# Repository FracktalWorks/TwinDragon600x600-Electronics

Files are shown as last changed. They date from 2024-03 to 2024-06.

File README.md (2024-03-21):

# TwinDragon600x600-Electronics
Electronic description, pinout and manuals for the electronics used in Twin Dragon 600x600x600 (Enhanced Size)

### For the Combination of BTT Manta M8P V2.0 + RPi CM4 + RP2040 based toolboard

Pin Configurations, jumper selection, CanBus and multi-MCU wiring to RPi CM4 embedded onto BTT Manta M8P V2.0 for Twin Dragon 600x600x600

Components used:
1. BTT Manta M8P V2.0 - 1
2. RPi CM4 (embed onto BTT Manta M8P V2.0) - 1
3. RP2040 based Can Module/Toolboard - 2
4. TMC5160 Stepper drivers - 4
5. TMC5160T Plus Z driver - 1
6. TMC2209 stepper drivers - 2 (External) + 2 (Present on the Toolboards)
7. BTT HDMI5 Touch Display

## Setting up BTT Manta M8P V2.0 + RPi CM4 + RP2040 based toolboard

After powering on the M8P, the LED on the bottom left corner will light up to indicate normal power supply. The VUSB jumper in the center is for selecting power - it should only be shorted when powering the board via USB or supplying power out via USB.



### Other Initial preparation and setting up jumpers

#### TMC Driver SPI Mode



The first row are the defined pin for the drivers, which are either high or low when shorted or unshorted to establish different mode of communication. The second row are defined with the SPI modes, with the namings of 'MISO', 'CS', 'SCK' and 'MOSI' when read from left to right. Since we use the TMC5160 driver, it specifically operates only on the SPI mode. Insert the jumpers corresponding to its parallel pins only on the 1st and the 2nd row as shown in the image.

#### TMC Driver UART Mode



The given set of pin to short is the CS pin that enables only the uart mode.

#### Driver Voltage selection

For High Voltage selection(48V):



Since the TMC5160 operates only on SPI mode, which is specifically for achieving faster communication and higher speeds, it needs an operating voltage of around 48V. The manta M8P has seperte pins for regular voltage of 24V and high voltage of 48V, that is to be jumped to the common pin of voltage supply to the drivers. We jump the HV pin in the left to the middle pin of supply in order to provide 48V to the drivers, as shown in the image above.

For normal Voltage selection (24V):



This voltage selection can be used when using a regular TMC2209 on the UART mode

#### Setting up jumper for probe activation

BTT Manta M8P V2 0 ABL Connections

The pin for probe used here is the IND-probe pin on Manta M8P V2.0, and the jumpers are placed on the two pins beside the probe pins, and other three perpendicular pins to its right, where the top two are to jumped together to activate the probe pin, as shown in the image above, to enable 24V/5V supply to the ABL board. The three columns of the pins starting from the top are 5V, 12V, 24V Respectively.

#### Setting up Jumper for CANBUS communication



At the left of the CAN pin, a small jumper is to be placed on the pins that mention '120R' depicting the 120 ohms resistance that is applied on the CAN Low and High communication pins. This is a crucial pin for the setting up of the CAN communication of the motherboard and toolboard.

## Wiring and Connections

Twin Dragon 600 CM4 M8P V2 0 - Wiring

The overall connections of all the Electrical and Electronic components are present in the image above

### BTT Manta M8P V2.0 Pin connections

Twin Dragon 600x600 with M8P V2 0 Wiring

## Dragon ToolBoard Pinout Mappings

WhatsApp Image 2024-03-20 at 14 31 21

WhatsApp Image 2024-03-20 at 14 31 21 (1)

## Guide to place the connectors on the Carriage Minifit Board

minifit board guide

## To setup Raspeberry Pi camera Rev 1.3, interfaced with RPi CM4 and BTT Manta M8P/M5P

In order to interface the Pi camera Rev 1.3 with the RPi CM4 and BTT Manta M8P/M5P, flip the board and check for a CSI1 camera slot, which should look like the image below



Instructions to attach the camera in BTT Manta M8P V2.0



Instructions to attach the camera in BTT Manta M8P V2.0

1. Now, boot up the board (including CM4), SSH into the CM4 and open the terminal
2. We will have to download a bin file into the boot folder of the CM4, below is the command to enter into the terminal.

`sudo wget https://datasheets.raspberrypi.com/cmio/dt-blob-cam1.bin -O /boot/dt-blob.bin`

If the above command does not work, try the following command:

`sudo wget https://datasheets.raspberrypi.com/cmio/dt-blob-cam1.bin -O /boot/firmware/dt-blob.bin`

3. Now, in the terminal, enter `sudo raspi-config` and select the option '3 Interface Options    Configure connections to peripherals'. Now select the first option 'P1 Camera      Enable/disable connection to the Raspberry Pi Camera'. A pop-up would appear where it asks to enable the camera. Make sure to select <yes> and exit the portal.

4. Now, in the terminal, type in `sudo nano /boot/config.txt` and make sure the settings are enabled

   `start_x=1
   gpu_mem=128`

   Note: make sure `#camera_auto_select=1` is commented out, or else it will not work.

For more clarifications, check out 'Julia TouchUI documentation' for more settings on Pi-camera

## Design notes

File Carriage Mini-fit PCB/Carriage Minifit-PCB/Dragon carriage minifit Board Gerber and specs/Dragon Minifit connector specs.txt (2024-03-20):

Dragon Carriage Board connector: 
 
Connector: 
Molex 6P 2x3 Minifit Jr. 4.2mm Connector: 
https://www.sunrom.com/p/6p-2x3-minifit-42mm-straight-female-pcb-header  
 
Housing: 
Molex 6P 2x3 Minifit Jr. 4.2mm Housing: 
https://www.sunrom.com/p/6p-2x3-minifit-42mm-male-housing  
 
Crimp Terminals: 
Molex 6P 2x3 Minifit Jr. 4.2mm Crimps: 
https://www.sunrom.com/p/crimping-pins-for-male-housing-minifit-42mm

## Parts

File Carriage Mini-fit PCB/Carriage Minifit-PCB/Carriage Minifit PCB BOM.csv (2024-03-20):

Qty | Designator | Footprint | Comment | LCSC Part # | Description | Value
1 | J1 | MOLEX_39281063 | 39281063 |  | Conn Wire to Board HDR 6Power POS 4.2mm Solder ST Top Entry Thru-Hole Mini-Fit Jr Bag Check availability | 39281063
1 | X1 | JST-XH-02-PACKAGE-LONG-PAD | JST-XH-02-PIN-LONG-PAD |  | JST XH Connector 2 Pin | JST-XH-02-PIN-LONG-PAD
1 | X2 | TERMINAL-BLOCK-4-PIN-3.5MM-LONG-PAD | TERMINAL-BLOCK-3.5MM-4-PIN-LONG-PAD |  | Terminal Block 3.5mm | TERMINAL-BLOCK-3.5MM-4-PIN-LONG-PAD

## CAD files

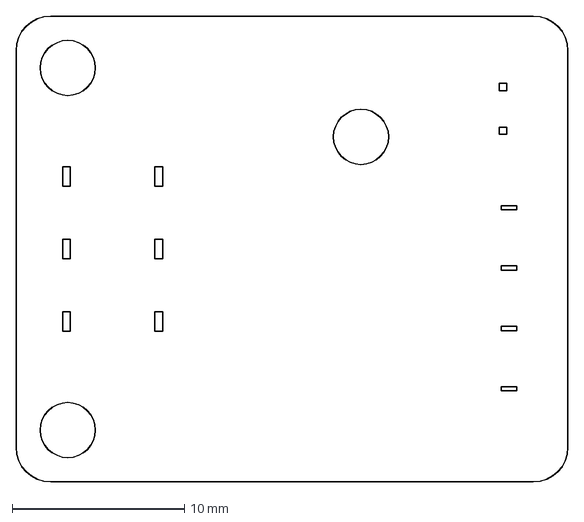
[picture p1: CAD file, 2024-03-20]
Carriage Mini-fit PCB/TD Carriage MINIFIT board.dxf
32.0 x 27.0 mm

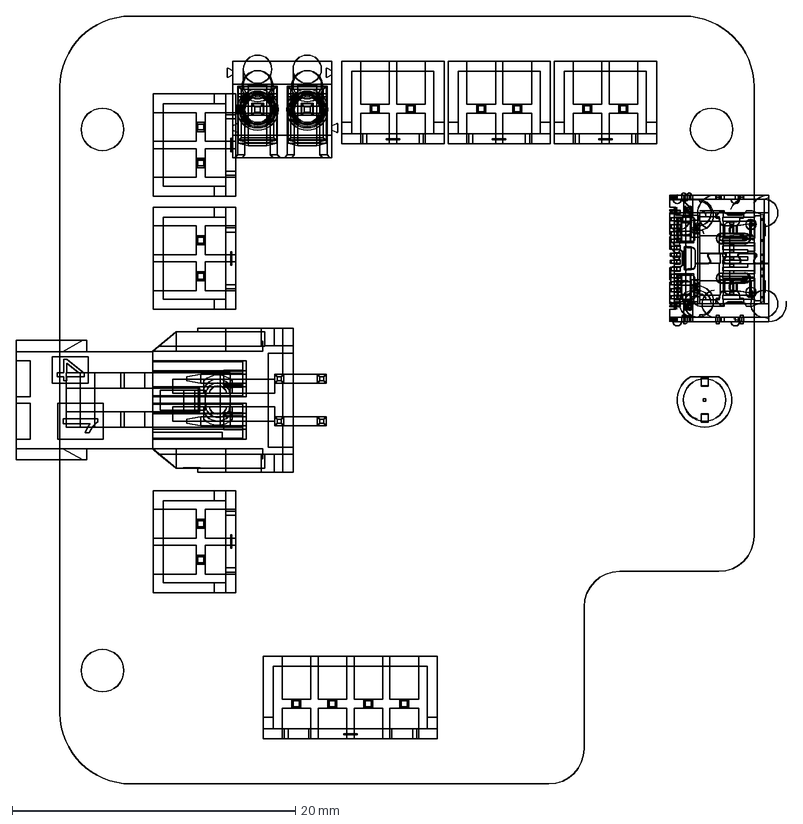
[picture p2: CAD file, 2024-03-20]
TD_Tool Board V2/PCB V2.1.dxf
54.4 x 54.2 mm

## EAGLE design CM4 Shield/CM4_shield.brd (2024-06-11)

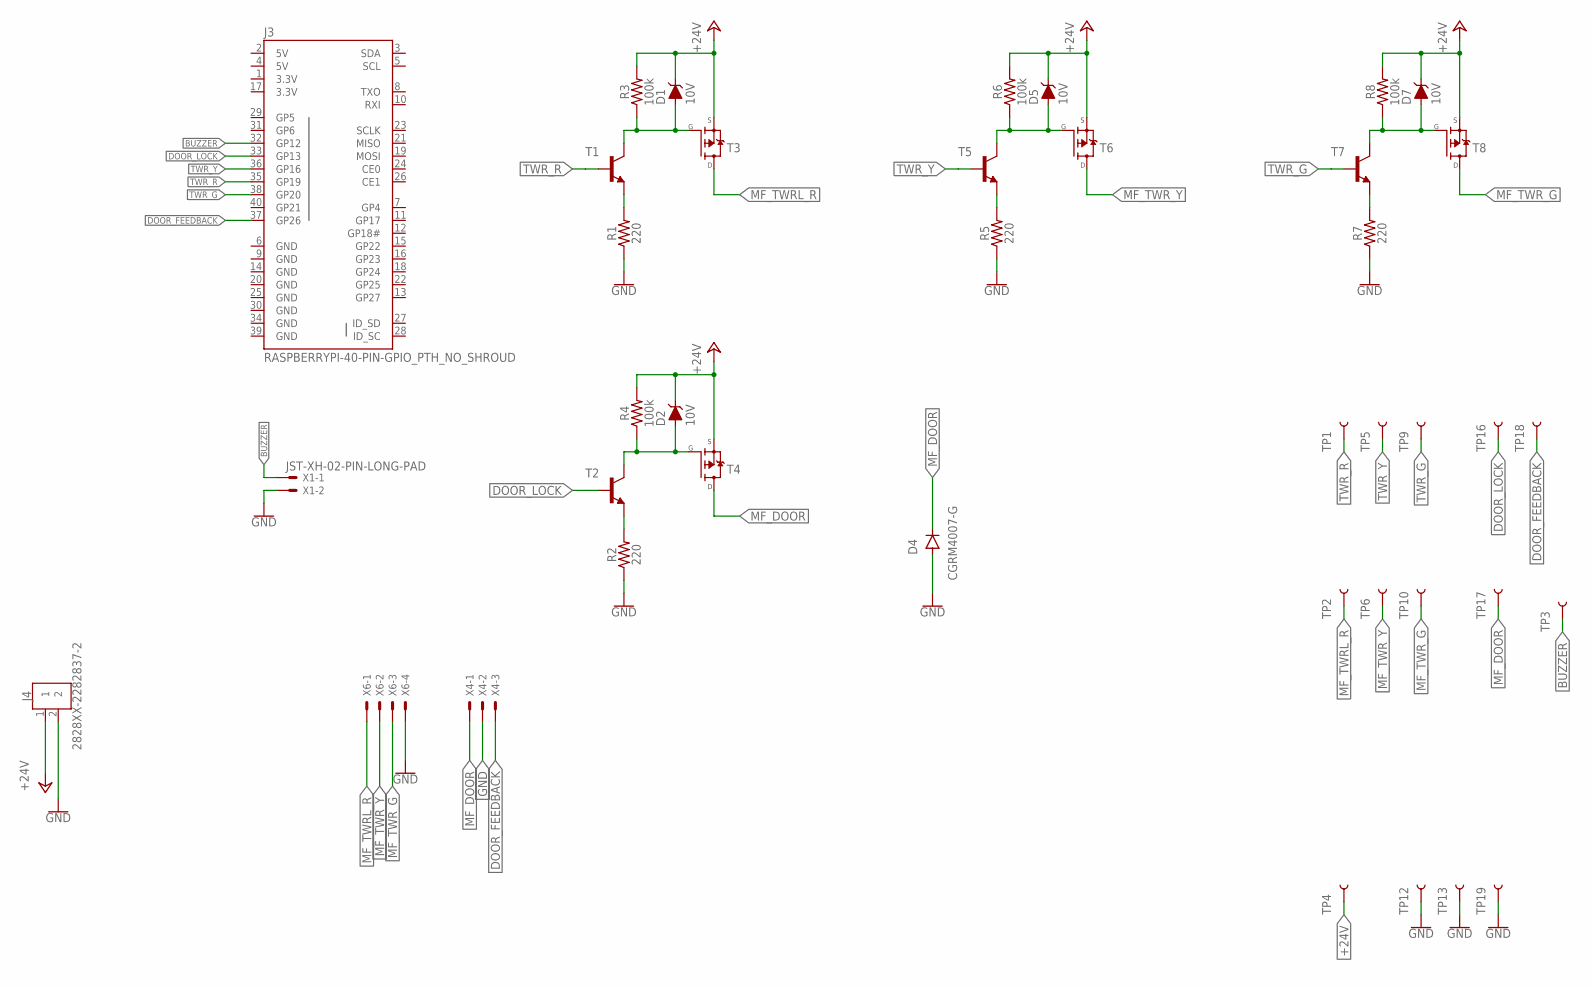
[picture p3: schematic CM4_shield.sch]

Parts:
D1, D2, D5, D7: 10V; PANASONIC_SMINI2-F5-B
D4: CGRM4007-G; SOD-123_MINI-SMA
J3: RASPBERRYPI-40-PIN-GPIO_PTH_NO_SHROUD; 2X20
J4: 2828XX-2282837-2; TERMBLK_508-2N
R1, R2, R5, R7: 220; 0603
R3, R4, R6, R8: 100k; 0603
T1, T2, T5, T7: MMBT3904LT1-NPN-SOT23-BEC; SOT23-BEC
T3, T4, T6, T8: MOSFET_P_SOT223; MOSFET_SOT223
TP1, TP2, TP3, TP4, TP5, TP6, TP9, TP10, TP12, TP13, TP16, TP17, TP18, TP19: TEST-POINT3X5; PAD.03X.05
X1: JST-XH-02-PIN-LONG-PAD; JST-XH-02-PACKAGE-LONG-PAD
X4: DOOR LOCK; JST-XH-03-PACKAGE-LONG-PAD
X6: TOWER LIGHT; JST-XH-04-PACKAGE-LONG-PAD

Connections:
3.3V: J3.1 (3.3V), J3.17 (3.3V)
5V: J3.2 (5V), J3.4 (5V)
+24V: D1.C, D2.C, D5.C, D7.C, J4.1, R3.2, R4.2, R6.2, R8.2, T3.3 (S), T4.3 (S), T6.3 (S), T8.3 (S), TP4.P$1
BUZZER: J3.32 (GP12), TP3.P$1, X1.1
DOOR_FEEDBACK: J3.37 (GP26), TP18.P$1, X4.3
DOOR_LOCK: J3.33 (GP13), T2.B, TP16.P$1
GND: D4.A, J3.6 (GND), J3.9 (GND), J3.14 (GND), J3.20 (GND), J3.25 (GND), J3.30 (GND), J3.34 (GND), J3.39 (GND), J4.2, R1.1, R2.1, R5.1, R7.1, TP12.P$1, TP13.P$1, TP19.P$1, X1.2, X4.2, X6.4
MF_DOOR: D4.C, T4.2 (D), T4.4 (D), TP17.P$1, X4.1
MF_TWRL_R: T3.2 (D), T3.4 (D), TP2.P$1, X6.1
MF_TWR_G: T8.2 (D), T8.4 (D), TP10.P$1, X6.3
MF_TWR_Y: T6.2 (D), T6.4 (D), TP6.P$1, X6.2
unnamed: R1.2, T1.E
unnamed: D5.A, R6.1, T5.C, T6.1 (G)
unnamed: D1.A, R3.1, T1.C, T3.1 (G)
unnamed: R5.2, T5.E
unnamed: D7.A, R8.1, T7.C, T8.1 (G)
unnamed: R7.2, T7.E
unnamed: D2.A, R4.1, T2.C, T4.1 (G)
unnamed: R2.2, T2.E
TWR_G: J3.38 (GP20), T7.B, TP9.P$1
TWR_R: J3.35 (GP19), T1.B, TP1.P$1
TWR_Y: J3.36 (GP16), T5.B, TP5.P$1

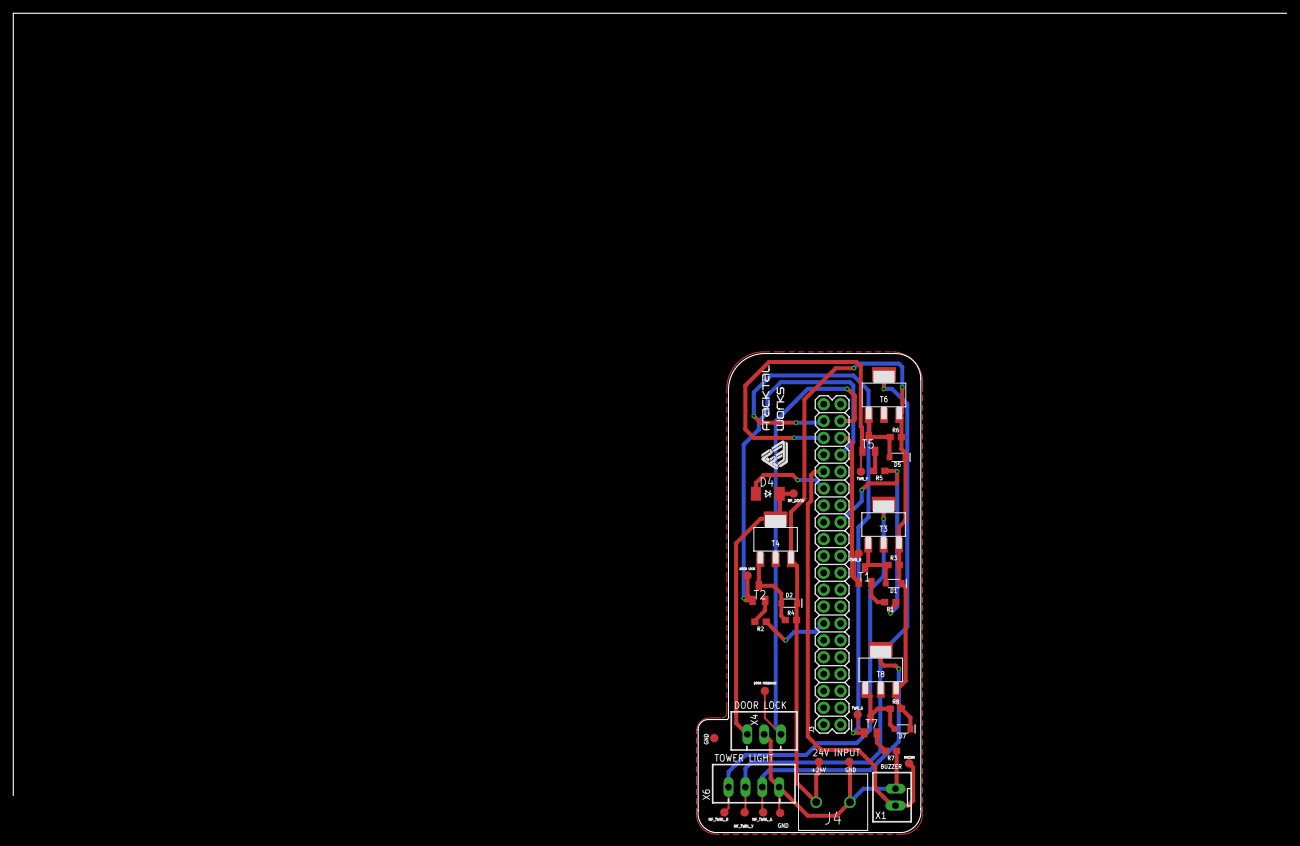
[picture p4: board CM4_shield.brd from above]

Board: 2 copper layers, 33.6 x 72.1 mm, 41 parts (0 on the bottom side), 22 nets.

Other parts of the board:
U$1: FWLOGO_SMALL

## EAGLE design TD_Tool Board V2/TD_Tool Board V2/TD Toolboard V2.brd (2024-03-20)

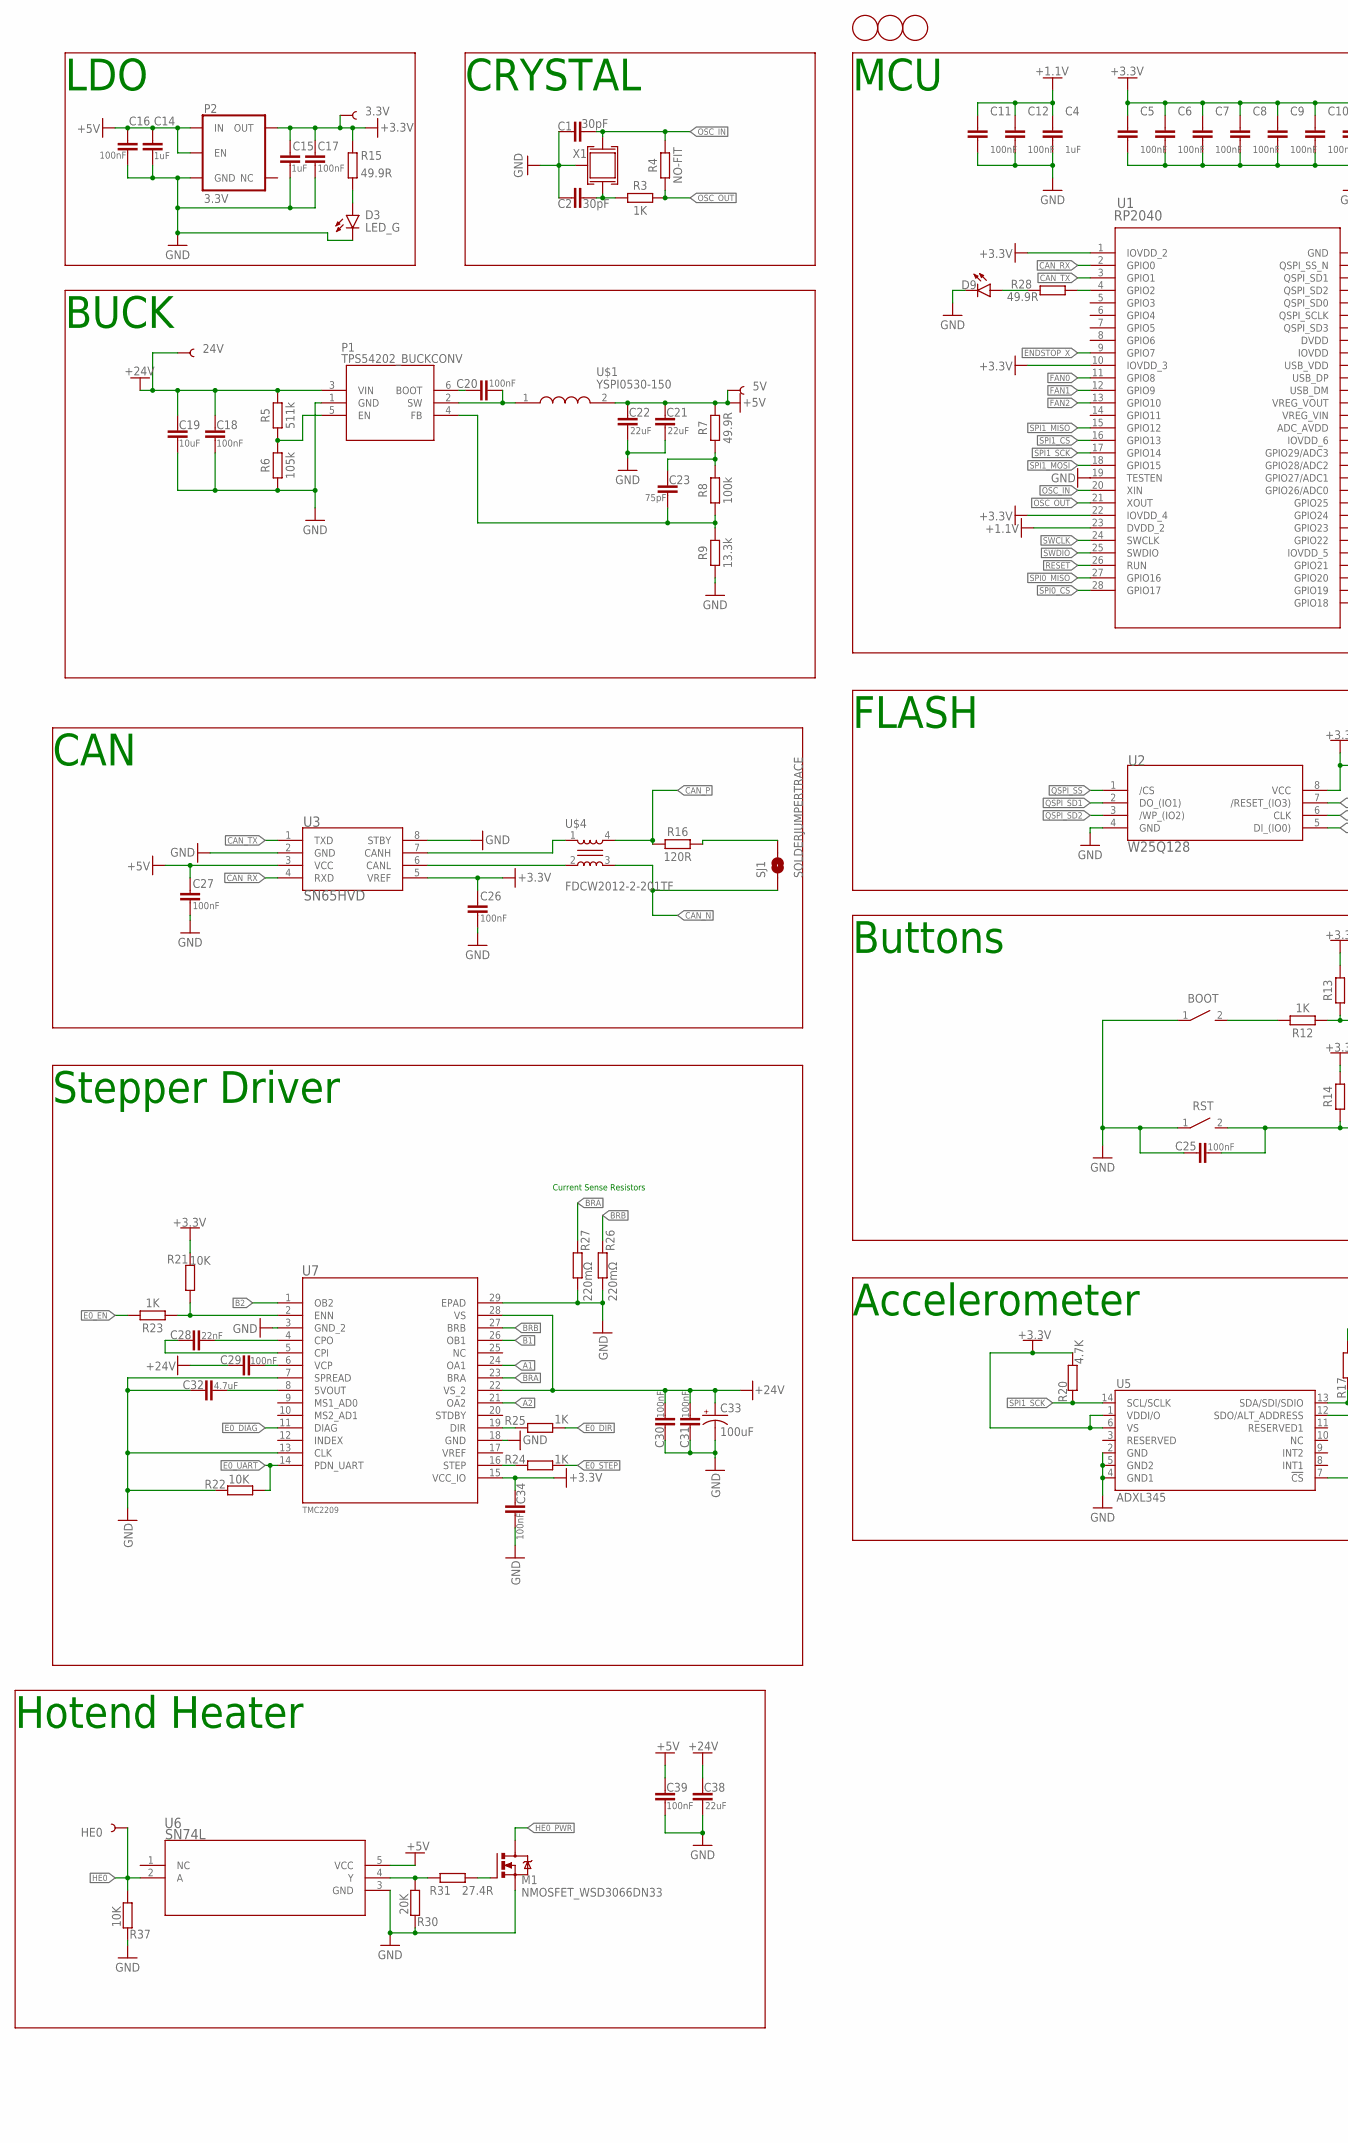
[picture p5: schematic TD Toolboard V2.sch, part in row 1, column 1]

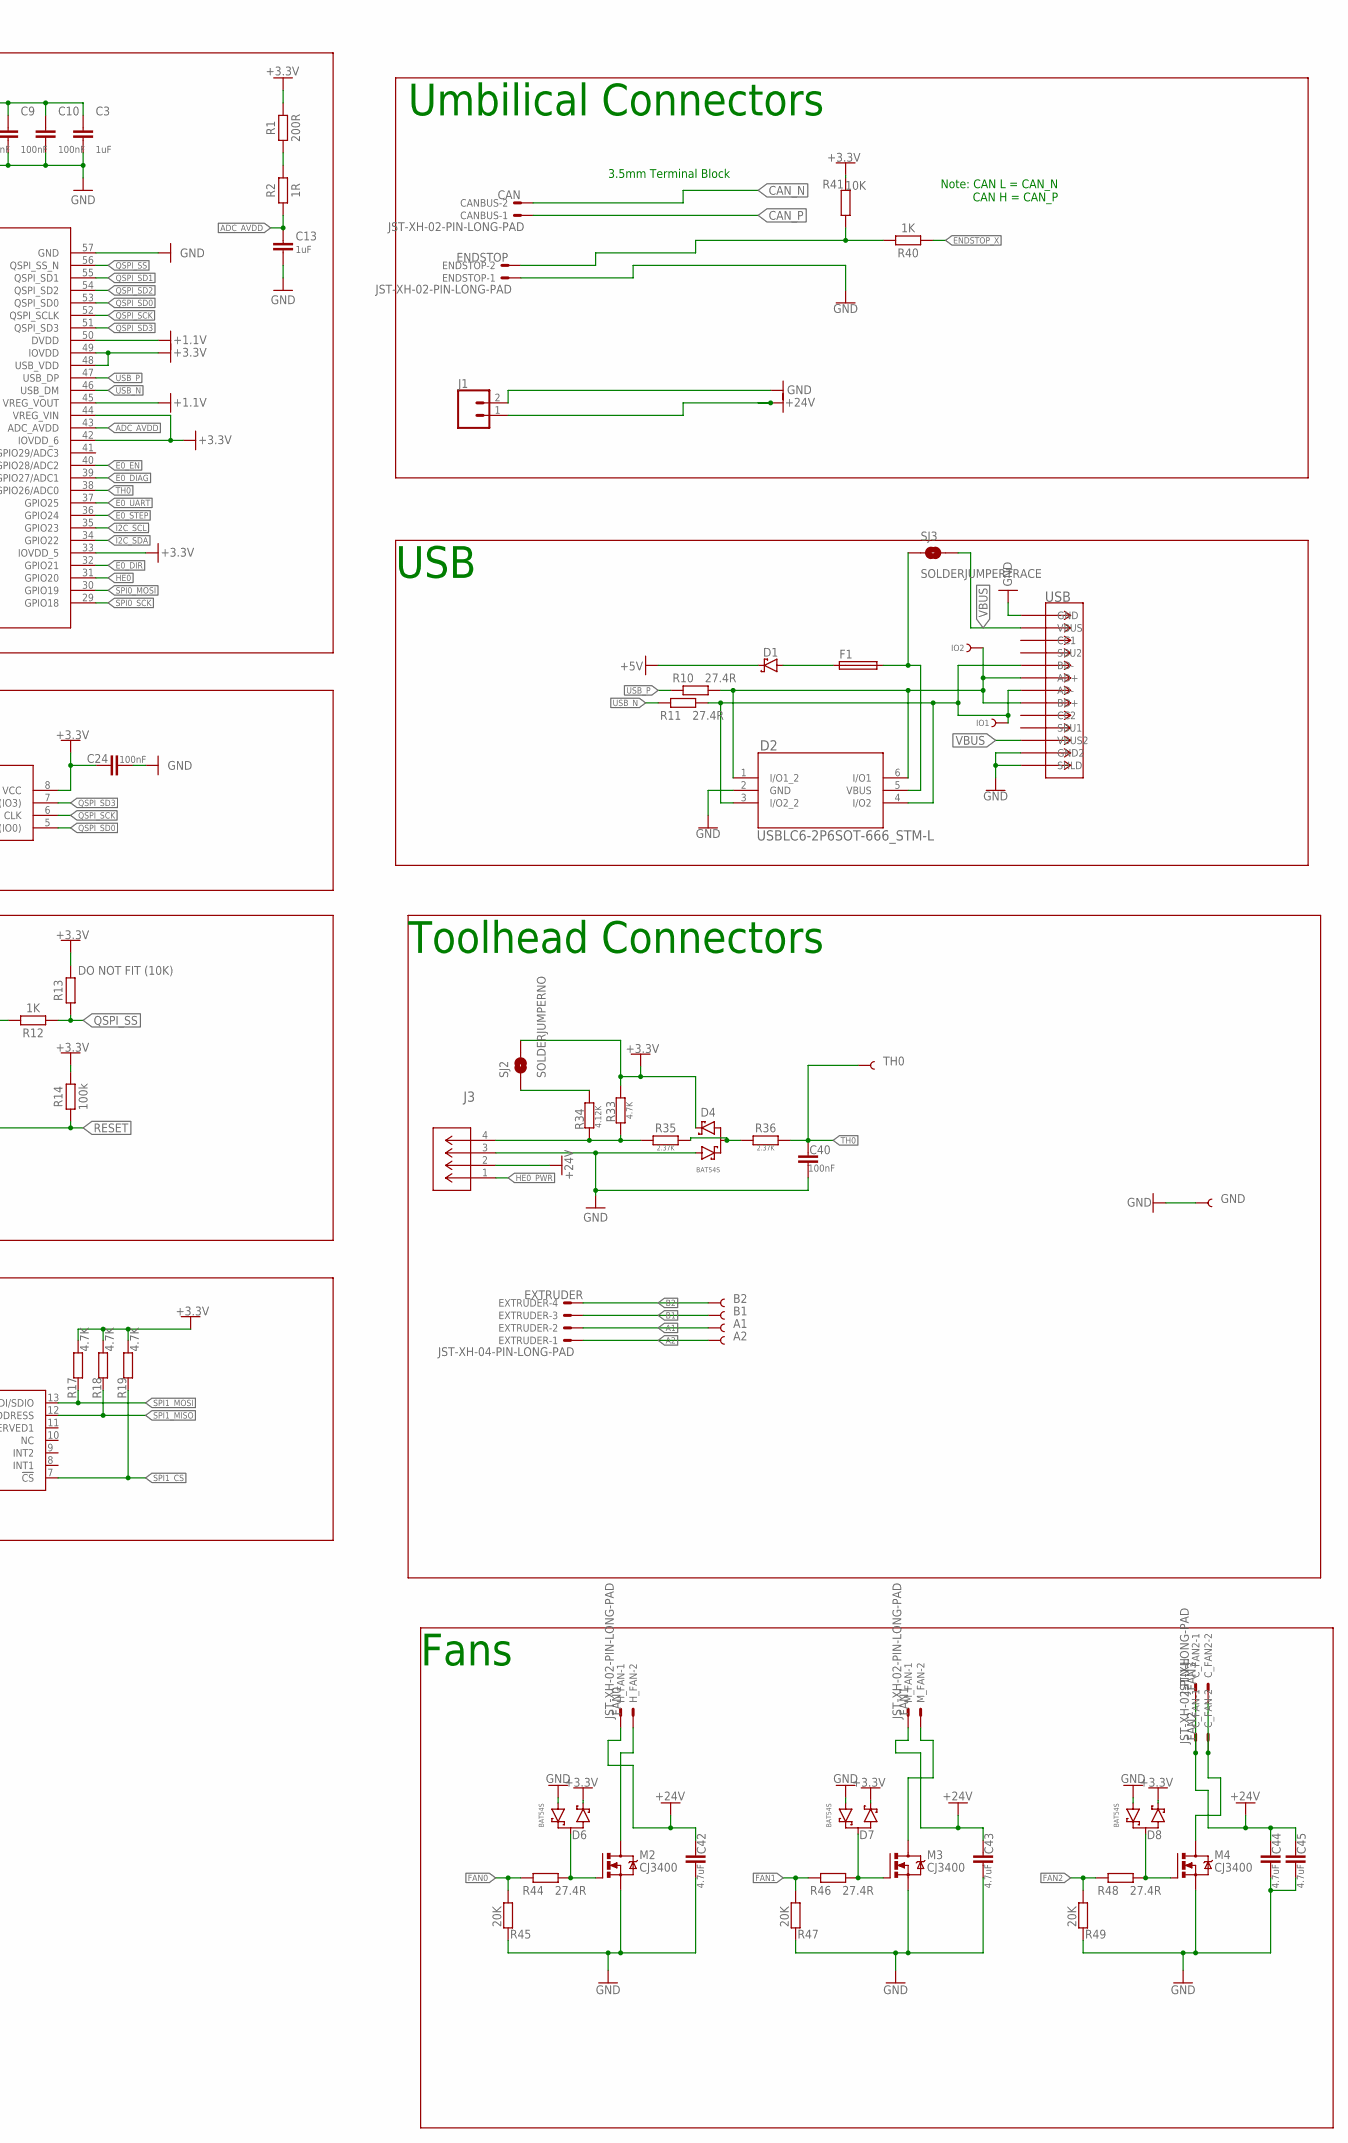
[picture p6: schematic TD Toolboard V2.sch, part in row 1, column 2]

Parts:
3.3V, 5V, 24V: TEST-POINT3X4; PAD.03X.04
A1, A2: TEST-POINT3X4; PAD.03X.04
B1, B2: TEST-POINT3X4; PAD.03X.04
BOOT: B3U-1000P(M)-B; LCSCPN# C231329
C1, C2: 30pF; CAPC1005X60; LCSCPN# C1570
C3, C4, C13, C14, C15: 1uF; CAPC1005X60; LCSCPN# C52923
C5, C6, C7, C8, C9, C10, C11, C12, C16, C17, C18, C20, C24, C25, C26, C27, C29, C30, C31, C34, C39, C40: 100nF; CAPC1005X60; LCSCPN# C307331
C19: 10uF; CAPC1608X85; LCSCPN# C194427
C21, C22, C38: 22uF; CAPC2012X110; LCSCPN# C338080
C23: 75pF; CAPC1005X60; LCSCPN# C37809
C28: 22nF; CAPC1005X60; LCSCPN# C1532
C32, C42, C43, C44, C45: 4.7uF; CAPC1608X85; LCSCPN# C162274
C33: 100uF; PANASONIC_D; LCSCPN# C128464
CANBUS: JST-XH-02-PIN-LONG-PAD; JST-XH-02-PACKAGE-LONG-PAD
C_FAN: JST-XH-02-PIN-LONG-PAD; JST-XH-02-PACKAGE-LONG-PAD
C_FAN2: JST-XH; JST-XH-02-PACKAGE-LONG-PAD
D1: MBR0520LT1G; SODFL3718X115
D2: USBLC6-2P6SOT-666_STM-L; SOT-666_STM-L; LCSCPN# C2827693
D3: LED_G; LEDC1608X35N_FLAT-G; LCSCPN# C72043
D4, D6, D7, D8: BAT54S; SOT23; LCSCPN# C47546
D9: LED_G; LED3MM; LCSCPN# C72043
ENDSTOP: JST-XH-02-PIN-LONG-PAD; JST-XH-02-PACKAGE-LONG-PAD
EXTRUDER: JST-XH-04-PIN-LONG-PAD; JST-XH-04-PACKAGE-LONG-PAD
F1: FUSE_CHIP-0603(1608-METRIC); FUSC1608X60N; LCSCPN# C261937
FD4, FD5, FD6: FIDUCIAL; FIDUCIAL_1MM
GND: TEST-POINT3X4; PAD.03X.04
HE0: TEST-POINT3X4; PAD.03X.04
H_FAN: JST-XH-02-PIN-LONG-PAD; JST-XH-02-PACKAGE-LONG-PAD
IO1, IO2: TEST-POINT3; PAD.03X.03
J1: CONN_023.5MM; SCREWTERMINAL-3.5MM-2
J3: JST-MICROFIT; CON_430450400_MOL
M1: NMOSFET_WSD3066DN33; LCSCPN# C148386
M2, M3, M4: CJ3400; SOT23; LCSCPN# C19019
M_FAN: JST-XH-02-PIN-LONG-PAD; JST-XH-02-PACKAGE-LONG-PAD
P1: TPS54202_BUCKCONV; SOT-23-6; LCSCPN# C191884
P2: 3.3V; SOT23-5; LCSCPN# C51118
R1: 200R; RESC1005X40; LCSCPN# C25087
R2: 1R; RESC1005X40; LCSCPN# C25086
R3, R12, R23, R24, R25, R40: 1K; RESC1005X40; LCSCPN# C25543
R4: NO-FIT; RESC1005X40; LCSCPN# NO-FIT
R5: 511k; RESC1005X40; LCSCPN# C3037035
R6: 105k; RESC1005X40; LCSCPN# C2933067
R7, R15, R28: 49.9R; RESC1005X40; LCSCPN# C25120
R8, R14: 100k; RESC1005X40; LCSCPN# C25741
R9: 13.3k; RESC1005X40; LCSCPN# C2974007
R10, R11, R31, R44, R46, R48: 27.4R; RESC1005X40; LCSCPN# C31439
R13: DO NOT FIT (10K); RESC1005X40; LCSCPN# NO-FIT
R16: 120R; RESC1005X40; LCSCPN# C25079
R17, R18, R19, R20, R33: 4.7K; RESC1005X40; LCSCPN# C304616
R21, R22, R37, R41: 10K; RESC1005X40; LCSCPN# C25744
R26, R27: 220mΩ; RESC1005X40; LCSCPN# C705474
R30, R45, R47, R49: 20K; RESC1005X40; LCSCPN# C25765
R34: 4.12K; RESC1005X40; LCSCPN# C227106
R35, R36: 2.37K; RESC1005X40; LCSCPN# C425373
RST: B3U-1000P(M)-B; LCSCPN# C231329
SJ1, SJ3: SOLDERJUMPERTRACE; SJ_2S-TRACE
SJ2: SOLDERJUMPERNO; SJ_2S-NO
TH0: TEST-POINT3X4; PAD.03X.04
U1: RP2040; IC57_RP2040-L; LCSCPN# C2040
U2: W25Q128; SOIC_128JVSIQ_WIN-L; LCSCPN# C97521
U3: SN65HVD; D8-L; LCSCPN# C14019
U5: ADXL345; ADXL345_LGA14; LCSCPN# C9667
U6: SN74L; DBV5-L; LCSCPN# C7836
U7: TMC2209; QFN28_5X5_3X8_EPAD_TRI; LCSCPN# C2150710
U$1: YSPI0530-150
U$4: FDCW2012-2-201TF
USB: USB-C(KH-TYPE-C-16P); CONN12_KH-TYPE-C-16P; LCSCPN# C709357
X1: CRYSTAL_TAXM12M4RLBDDT2T_3225; CRYSTAL_3225; LCSCPN# C133334

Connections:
+1.1V: C4.1, C11.1, C12.1, U1.23 (DVDD_2), U1.45 (VREG_VOUT), U1.50 (DVDD)
+3.3V: 3.3V.P$1, C3.1, C5.1, C6.1, C7.1, C8.1, C9.1, C10.1, C15.1, C17.1, C24.1, C26.1, C34.1, D4.2, D6.2, D7.2, D8.2, P2.5 (OUT), R1.2, R13.2, R14.2, R15.2, R17.2, R18.2, R19.2, R20.2, R21.1, R33.2, R41.1, SJ2.2, U1.1 (IOVDD_2), U1.10 (IOVDD_3), U1.22 (IOVDD_4), U1.33 (IOVDD_5), U1.42 (IOVDD_6), U1.44 (VREG_VIN), U1.48 (USB_VDD), U1.49 (IOVDD), U2.8 (VCC), U3.5 (VREF), U5.1 (VDDI/O), U5.6 (VS), U7.15 (VCC_IO)
+5V: 5V.P$1, C14.1, C16.1, C21.1, C22.1, C27.1, C39.1, D1.1 (C), P2.1 (IN), P2.3 (EN), R7.2, U3.3 (VCC), U6.5 (VCC), U$1.2
+24V: 24V.P$1, C18.1, C19.1, C29.1, C30.2, C31.2, C33.+, C38.1, C42.1, C43.1, C44.1, C45.1, C_FAN.1, C_FAN2.1, H_FAN.1, J1.1, J3.2, M_FAN.1, P1.3 (VIN), R5.2, U7.22 (VS_2), U7.28 (VS)
A1: A1.P$1, EXTRUDER.2, U7.24 (OA1)
A2: A2.P$1, EXTRUDER.1, U7.21 (OA2)
ADC_AVDD: C13.1, R2.1, U1.43 (ADC_AVDD)
ADC_R: R1.1, R2.2
B1: B1.P$1, EXTRUDER.3, U7.26 (OB1)
B2: B2.P$1, EXTRUDER.4, U7.1 (OB2)
BCBOOT: C20.1, P1.6 (BOOT)
BRA: R27.2, U7.23 (BRA)
BRB: R26.2, U7.27 (BRB)
CAN1_N: U3.6 (CANL), U$4.2
CAN1_P: U3.7 (CANH), U$4.1
CAN_N: CANBUS.2, SJ1.1, U$4.3
CAN_P: CANBUS.1, R16.1, U$4.4
CAN_RX: U1.2 (GPIO0), U3.4 (RXD)
CAN_TX: U1.3 (GPIO1), U3.1 (TXD)
CNT: R16.2, SJ1.2
DIR: R25.2, U7.19 (DIR)
E0_DIAG: U1.39 (GPIO27/ADC1), U7.11 (DIAG)
E0_DIR: R25.1, U1.32 (GPIO21)
E0_EN: R23.2, U1.40 (GPIO28/ADC2)
E0_STEP: R24.1, U1.36 (GPIO24)
E0_UART: R22.2, U1.37 (GPIO25), U7.14 (PDN_UART)
ENDSTOP_X: R40.1, U1.9 (GPIO7)
EX: ENDSTOP.2, R40.2, R41.2
FAN0: R44.2, R45.2, U1.11 (GPIO8)
FAN0G: D6.3, M2.1 (G), R44.1
FAN1: R46.2, R47.2, U1.12 (GPIO9)
FAN1G: D7.3, M3.1 (G), R46.1
FAN2: R48.2, R49.2, U1.13 (GPIO10)
FAN2G: D8.3, M4.1 (G), R48.1
GND: BOOT.1, C1.2, C2.1, C3.2, C4.2, C5.2, C6.2, C7.2, C8.2, C9.2, C10.2, C11.2, C12.2, C13.2, C14.2, C15.2, C16.2, C17.2, C18.2, C19.2, C21.2, C22.2, C24.2, C25.1, C26.2, C27.2, C30.1, C31.1, C32.1, C33.-, C34.2, C38.2, C39.2, C40.2, C42.2, C43.2, C44.2, C45.2, D2.2 (GND), D3.C, D4.1, D6.1, D7.1, D8.1, D9.K (C), ENDSTOP.1, GND.P$1, J1.2, J3.3, M1.P$1 (S), M1.P$2 (S), M1.P$3 (S), M2.2 (S), M3.2 (S), M4.2 (S), P1.1 (GND), P2.2 (GND), R6.1, R9.1, R22.1, R26.1, R27.1, R30.1, R37.1, R45.1, R47.1, R49.1, RST.1, U1.19 (TESTEN), U1.57 (GND), U2.4 (GND), U3.2 (GND), U3.8 (STBY), U5.2 (GND), U5.4 (GND1), U5.5 (GND2), U6.3 (GND), U7.3 (GND_2), U7.7 (SPREAD), U7.13 (CLK), U7.18 (GND), U7.29 (EPAD), USB.1 (GND), USB.12 (GND2), USB.13 (SHLD), USB.14 (SHLD), USB.15 (SHLD), USB.16 (SHLD), USB.18 (SHLD), USB.19 (SHLD), USB.20 (SHLD), USB.21 (SHLD), USB.24 (SHLD), USB.25 (SHLD), USB.26 (SHLD), USB.27 (SHLD), USB.28 (SHLD), USB.29 (SHLD), USB.37 (SHLD), USB.39 (SHLD), USB.41 (SHLD), USB.43 (SHLD), X1.P$2 (GND), X1.P$4 (GND)
GPIOLED: D9.A, R28.1
HE0: HE0.P$1, R37.2, U1.31 (GPIO20), U6.2 (A)
HE0A: R30.2, R31.2, U6.4 (Y)
HE0B: M1.P$4 (G), R31.1
HE0_PWR: J3.1, M1.P$5 (D), M1.P$6 (D), M1.P$7 (D), M1.P$8 (D), M1.P$9 (D)
I2C_SCL: U1.35 (GPIO23)
I2C_SDA: U1.34 (GPIO22)
LDOLED: D3.A, R15.1
LED: R28.2, U1.4 (GPIO2)
unnamed: H_FAN.2, M2.3 (D)
unnamed: M3.3 (D), M_FAN.2
unnamed: C_FAN.2, C_FAN2.2, M4.3 (D)
OSC_IN: C1.1, R4.2, U1.20 (XIN), X1.P$1 (P1)
OSC_OUT: R3.2, R4.1, U1.21 (XOUT)
QSPI_SCK: U1.52 (QSPI_SCLK), U2.6 (CLK)
QSPI_SD0: U1.53 (QSPI_SD0), U2.5 (DI_(IO0))
QSPI_SD1: U1.55 (QSPI_SD1), U2.2 (DO_(IO1))
QSPI_SD2: U1.54 (QSPI_SD2), U2.3 (/WP_(IO2))
QSPI_SD3: U1.51 (QSPI_SD3), U2.7 (/RESET_(IO3))
QSPI_SS: R12.1, R13.1, U1.56 (QSPI_SS_N), U2.1 (/CS)
RESET: C25.2, R14.1, RST.2, U1.26 (RUN)
SPI0_CS: U1.28 (GPIO17)
SPI0_MISO: U1.27 (GPIO16)
SPI0_MOSI: U1.30 (GPIO19)
SPI0_SCK: U1.29 (GPIO18)
SPI1_CS: R19.1, U1.16 (GPIO13), U5.7 (!CS)
SPI1_MISO: R18.1, U1.15 (GPIO12), U5.12 (SDO/ALT_ADDRESS)
SPI1_MOSI: R17.1, U1.18 (GPIO15), U5.13 (SDA/SDI/SDIO)
SPI1_SCK: R20.1, U1.17 (GPIO14), U5.14 (SCL/SCLK)
STEP: R24.2, U7.16 (STEP)
SWB: BOOT.2, R12.2
SWCLK: U1.24 (SWCLK)
SWDIO: U1.25 (SWDIO)
TH0: C40.1, R36.2, TH0.P$1, U1.38 (GPIO26/ADC0)
TH0A: J3.4, R33.1, R34.1, R35.1
TH0B: D4.3, R35.2, R36.1
TH0C: R34.2, SJ2.1
TMC5V: C32.2, U7.8 (5VOUT)
TMCCPI: C28.1, U7.5 (CPI)
TMCCPO: C28.2, U7.4 (CPO)
TMCENN: R21.2, R23.1, U7.2 (ENN)
TMCVCP: C29.2, U7.6 (VCP)
USB1_N: D2.3 (I/O2_2), D2.4 (I/O2), IO1.P$1, R11.1, USB.5 (BD-), USB.7 (AD-)
USB1_P: D2.1 (I/O1_2), D2.6 (I/O1), IO2.P$1, R10.1, USB.6 (AD+), USB.8 (BD+)
USB_N: R11.2, U1.46 (USB_DM)
USB_P: R10.2, U1.47 (USB_DP)
VBUS: SJ3.2, USB.2 (VBUS), USB.11 (VBUS2)
VBUS1: D2.5 (VBUS), F1.2, SJ3.1
VBUS3: D1.2 (A), F1.1
VRC: C23.1, R7.1, R8.2
VREGEN: P1.5 (EN), R5.1, R6.2
VREGFB: C23.2, P1.4 (FB), R8.1, R9.2
VREGO: C20.2, P1.2 (SW), U$1.1
XR: C2.2, R3.1, X1.P$3 (P2)

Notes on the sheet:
LDO
BUCK
CRYSTAL
MCU
FLASH
Buttons
Accelerometer
CAN
Stepper Driver
Current Sense Resistors
Hotend Heater
Umbilical Connectors
Note: CAN L = CAN_N CAN H = CAN_P
3.5mm Terminal Block
USB
Toolhead Connectors
Fans

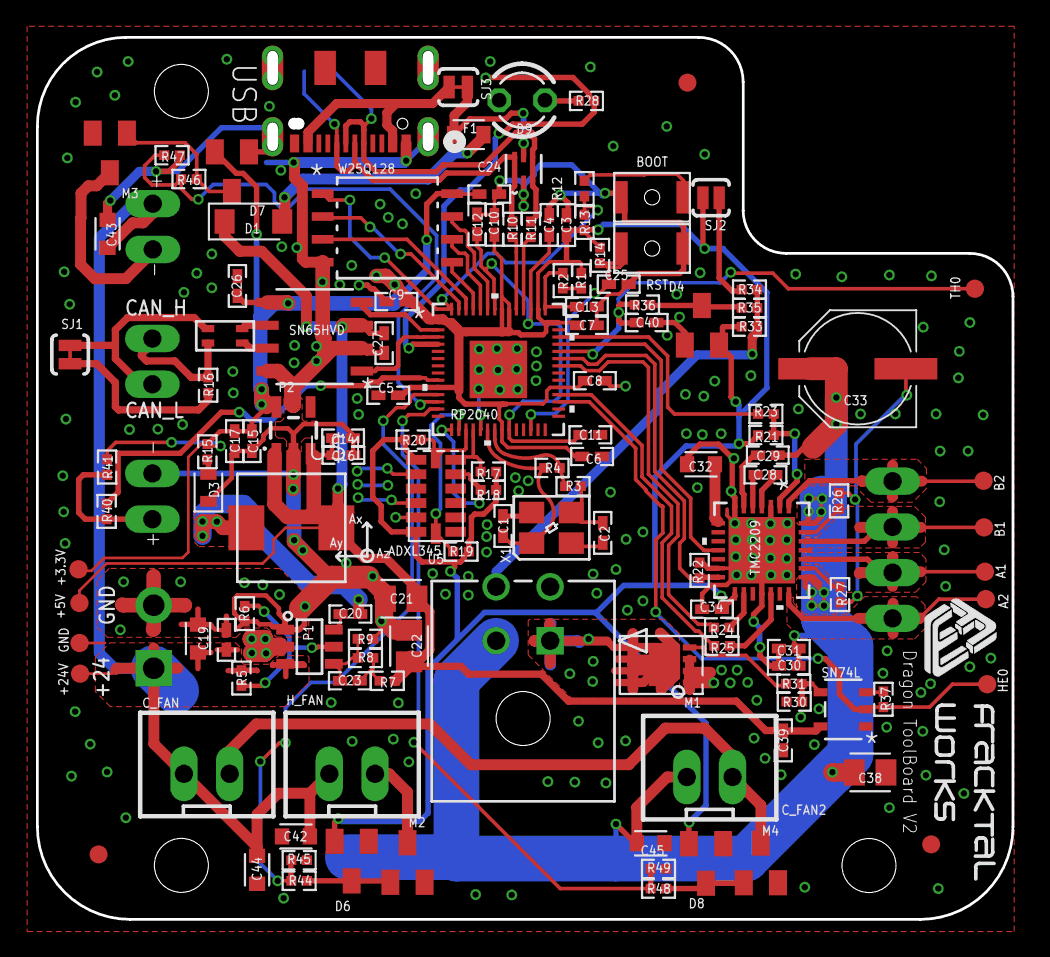
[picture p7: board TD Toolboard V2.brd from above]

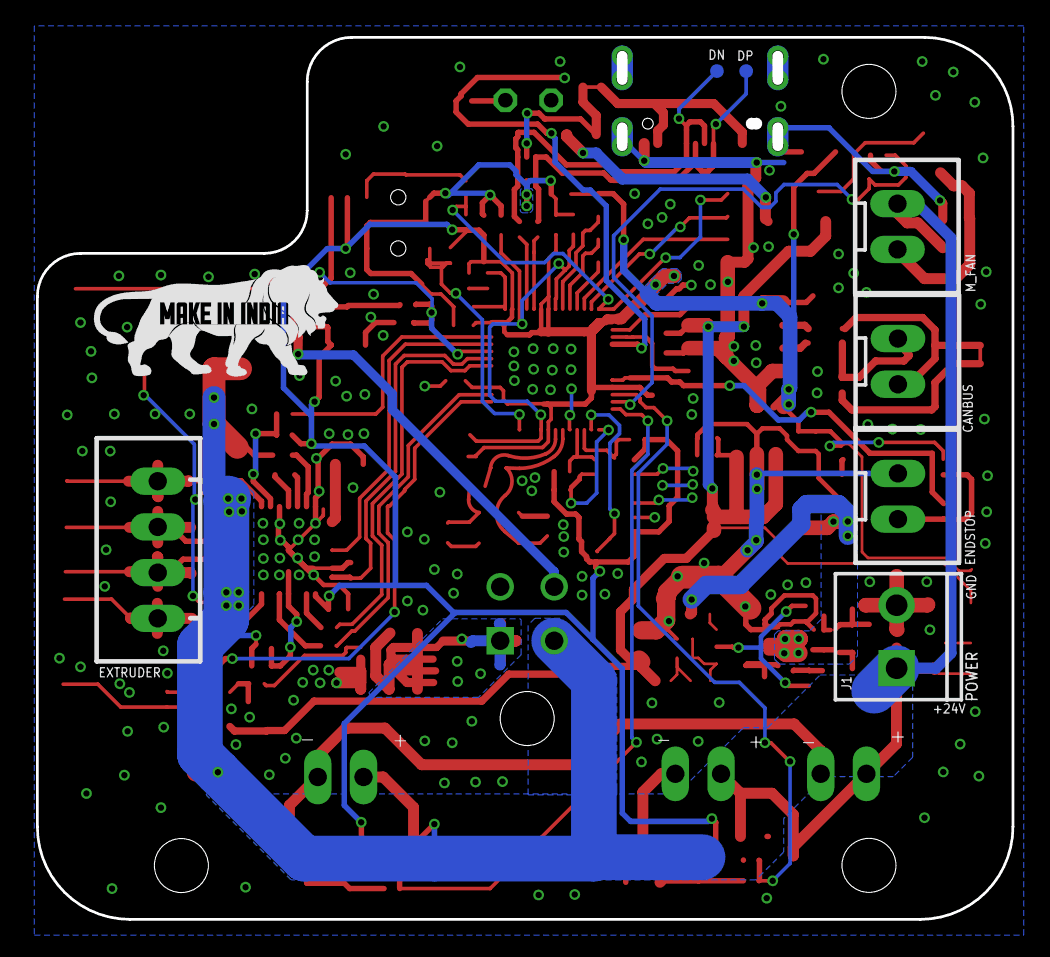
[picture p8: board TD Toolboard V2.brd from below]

Board: 2 copper layers, 54.2 x 49.0 mm, 140 parts (8 on the bottom side), 81 nets.

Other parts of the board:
U$2: MAKEININDIA
U$3: FWLOGO_SMALL

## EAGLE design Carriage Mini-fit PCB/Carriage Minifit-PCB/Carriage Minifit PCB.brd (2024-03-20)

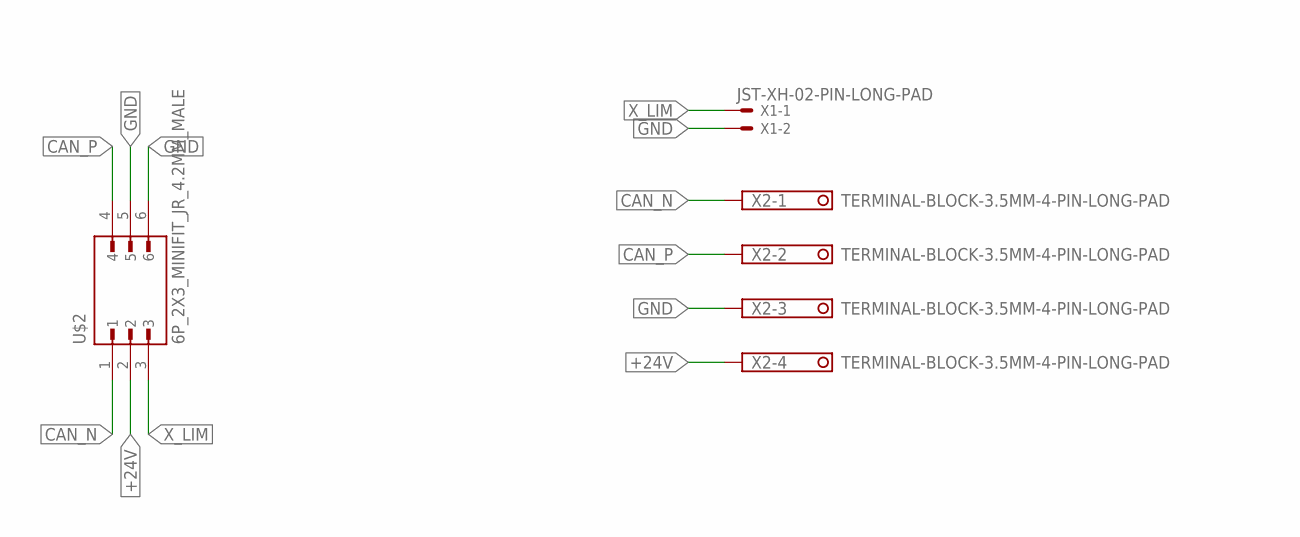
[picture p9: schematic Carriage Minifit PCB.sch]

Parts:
U$2: 6P_2X3_MINIFIT_JR_4.2MM_MALE
X1: JST-XH-02-PIN-LONG-PAD; JST-XH-02-PACKAGE-LONG-PAD
X2: TERMINAL-BLOCK-3.5MM-4-PIN-LONG-PAD; TERMINAL-BLOCK-4-PIN-3.5MM-LONG-PAD

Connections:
+24V: U$2.2, X2.4
CAN_N: U$2.1, X2.1
CAN_P: U$2.4, X2.2
GND: U$2.5, U$2.6, X1.2, X2.3
X_LIM: U$2.3, X1.1

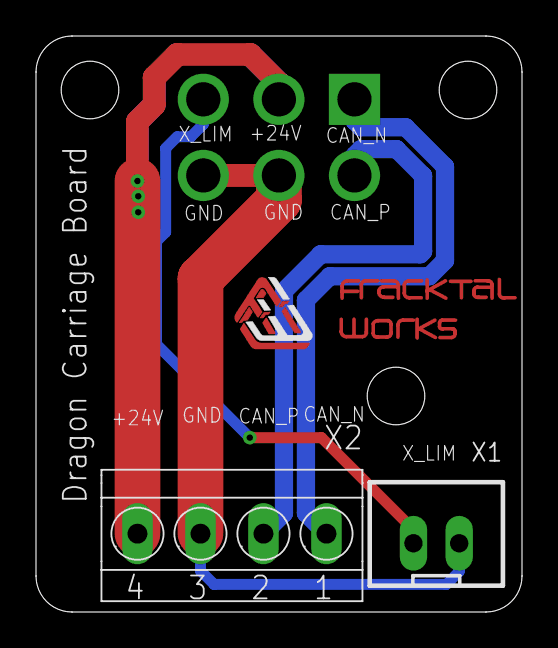
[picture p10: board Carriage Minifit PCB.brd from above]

Board: 2 copper layers, 27.0 x 32.0 mm, 4 parts (1 on the bottom side), 5 nets.

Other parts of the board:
U$1: FWLOGO_SMALL_FOOTPRINT; FWLOGO_SMALL

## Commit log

2024-03-20 Added datasheets, manuals and PCB files of relevant electronics used
    [Carriage Minifit PCB BOM.csv, Carriage Minifit PCB.brd, Carriage Minifit PCB.sch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]
2024-05-17 added CM4 shield board design files
    [CM4_shield.brd, CM4_shield.sch]
2024-05-18 Design updates
    [CM4_shield.brd]
2024-05-21 update to board design
    [CM4_shield.brd, CM4_shield.sch]
2024-06-11 Correction of DRC check, and changes accordingly
    [CM4_shield.brd]

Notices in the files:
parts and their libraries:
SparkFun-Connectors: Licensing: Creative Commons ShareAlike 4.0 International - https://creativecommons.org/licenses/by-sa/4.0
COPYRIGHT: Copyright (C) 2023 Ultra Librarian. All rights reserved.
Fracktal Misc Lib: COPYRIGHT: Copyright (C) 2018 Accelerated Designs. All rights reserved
